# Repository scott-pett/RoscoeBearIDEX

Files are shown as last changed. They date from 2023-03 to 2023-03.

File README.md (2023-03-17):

# Roscoe Bear IDEX 3D Printer

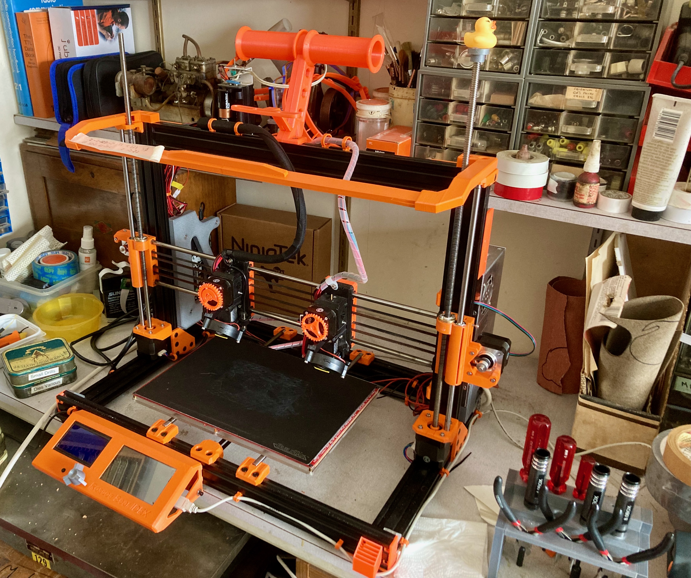
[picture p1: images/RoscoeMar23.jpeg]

__Roscoe Bear IDEX as of March 2023__

This is a remix of @gregsaun's excellent Prusa i3 Bear frame upgrade for the Prusa MK2 and MK3 printers.

I made it wider, taller and use most of the original Bear plastic parts to create a much longer X gantry to make room for a 300mm x 200mm bed and parking space for the two independant extruders. Print height is approximately 230mm, but I'm hoping to improve on that slightly without spending too much money.

# History
The design has been ongoing since 2017 or so and there is now a working prototype albeit lacking in certain features. The prototype has done useful work, but mainly as a single extruder printer :-)

Looking back at some of the design files, things have changed greatly from the earliest concept.

# Electronics and Firmware
The printer currently runs Marlin 2.1.3 and is controlled by a BTT Octopus V1.1 control board with TMC2130 and TMC2208 stepper drivers along with an ancient RepRap Full Graphics Display. A Raspberry Pi 3B+ acts as an Octoprint host and provides WiFi network connectivity and 4.3" touch screen with Octoscreen (or Octodash) for control. The printer can be operated from either screen and files printed from either SD card or via Octoprint. A CSI or USB webcam can be fitted if required.

# Klipper as an option
Of course, Klipper firmware could be used but I feel there would be few advantages except perhaps that of input shaping which has some better capabilities than Marlin2 current has. I doubt there would be much speed advantage being a "bed-slinger" although firmware updates would be more convenient than loading a microSD card into the slot after compiling Marlin in VScode - Horses for Courses.

If you decide to go down the Klipper firmware route, I would be interested in hearing how you get on.

# IDEX Carriages
The main departure from the Prusa Bear design is of course the X and U carriages (AKA: X and X2) which need to allow for the extra U (X2) stepper motor, belt and idler. For the moment this takes the form of taller X carriage components to make room for it all. The printed components comprise the XmotorUidler, UmotorXidler, Xcarriage and Ucarriage. The carriages are formed from two printed parts encapsulating some LM8UU linear bearings in fairly standard Prusa fashion. The arrangement allows for fairly easy assembly of the extruders to the carriages and also allows some early testing with just the carriages fitted. This keeps things fairly clear to setup homing, parking positions and check for clearances.

# Extruders
The X and U extruders are basically Prusa MK3S but with the wiring harness exiting the top of the units - there's not enough room between all the belts to provide the Prusaesque wiring egress. The endstop sensor boards will need their pins bending carefully so the three pin dupont socket attaches vertically rather horiontally. The rest of the assembly is pretty much as per Prusa's build instructions for the MK3S extruder with the ball bearing switched filament sensor. I have not used the earlier MK3 optical sensor variant which sensed filament movement.

The left hand extruder carries a PINDA2 probe for Z homing. This currently runs successfully at 3.3 volts with the spring steel flexplate. The righthand extruder being offset in the Marlin config to allow for any differences. At the moment, this means that the printer will only work in IDEX mode 1 - Auto Park. Mirroring and Cloning (modes 2 and 3) will not be highly successful. A SuperPINDA could be utilized instead. The benefit being that it is temperature compensated and does not rely on a separate thermister setup. So far the PINDA2 has worked fairly reliably.

Filament runout on both extruders is supported as per the Prusa setup. Just utilize a spare endstop port on the Octopus board - see Endstops

# Endstops
X, U and Y endstops are handled by the TMC2130 drivers (TMC2209 as an alternative). Z endstop is, as stated, a PINDA2 probe.

The Endstop configurationis as follows

    X - Xmin (Stallguard)
    U - Xmax (Stallguard)
    Y - Ymin (Stallguard)
    Z - Zmin (PINDA2)
    E0 runout - Zmax
    E1 runout - Ymax

# Thermisters
The BTT Octopus board allows for up to five thermisters. I have them as follows:

    T0 - Hotend 0
    T1 - Hotend 1
    T2 - Reserved for PINDA2 thermister
    T3 - Spare (Maybe for ambient sensor one day)
    TB - Heated Bed

# Heated Bed
The heated bed is a generic 24 volt 300mm x 200mm MK2-B (I think) with a BuildTak flexplate print surface from [3DJake](https://www.3djake.uk)

# Lighting
The Roscoe uses a string of NeoPixels arranged on a bracket above the bed. There is good Marlin support and only one pin is required from the control board. Indeed the BTT Octopus board has a dedicated NeoPixel pin. All that is required is a strong 5V supply to power it. I use a cheap eBay buck converter set to slightly above 5 volts. Marlin can be configured to provide printer events to generate various colours as the printer heats up and successfully completes a job. But this only works when printing from the SD card at the moment. From Octoprint you can just set appropriate commands in the Custom G-code routines to turn the lights on, off and different colours if you wish. Manual control via the menu is also available.

# Work To Do
1. Height adjustment for the U carriage and extruder so IDEX modes 2 and 3 can be used.

2. Purge buckets - and/or a far more reliable purge tower control to improve multi material print quality.

3. Move to Prusaslicer from Cura to improve print quality and simplify configuration - which requirest the next item:

4. Twin part fan control which - Prusaslicer doesn't generate - However, using a post process python script sensible part cooling fan control is available. See the Post Process page.

5. Shorten the height of the X and U carriage to increase the available print height.

6. Switch to a textured PEI sheet from the exisitng BuildTak setup

7. Finalize the Marlin2 config files.

# Alternatives
1. Control board could be a FYSETC Spider board - the Roscoe IDEX requires seven stepper motors to fully enable twin extruders and two independant Z motors. I did originally use an MKS RUMBA32 clone, but this only has support for six steppers and you have to do without the twin Z steppers and automatic gantry levelling. However this can be hacked reasonably well with a gcode script if a RUMBA32 or other six stepper board is all you have.

2. Stepper drivers could be TMC2209 for Stallguard on X, U and Y axis with TMC2208 for the extruders and Z motors. Although TMC have moved on now with driver options, the 22xx series drivers are more than adequate for the motor current requirement. You could always modify the endstop arrangement to something more tradiitonal if that is what you or your budget requires. There's nothing wrong with A4988 drivers and microswitch endstops. But I do like the quietness of the TMC drivers. You can hear the bearings squeak when they dry out!

3. Heated bed - In order to keep the weight down I have used a lightweight PCB heated bed with a flexible spring steel sheet system carrying a BuildTaK print surface. I originally inteneded to fit an aluminium bed carriage - Suitably laser or waterjet cut. But I started building the printer shortly before the first COVID lockdown in 2020 and getting special stuff made became quite difficult - as well as travelling around the country to collect parts. So, my Roscoe Bear IDEX has an acrylic bed carriage. I printed out the DXF outline and stuck it on a sheet of 5mm acrylic and got to work with drills and hacksaw. It is of course a lot lighter than an equivalent aluminium carriage although I doubt it would work too well in an enclosed casing as it would warp when it got hot. Marlin's BiLinear Mesh Bed Levelling appears to work sufficienty well for the moment. Of course a glass sheet and blue tape could be used if that is your preference but will increase the bed weight somewhat. Definitely a candidate for input shaping algorythms of some sort. My favourite, especially for PETG is a textured PEI surface which will be a future upgrade, once I find one - Maybe when the BuildTak surface wears out.

4. Extruder options are of course to use the E3D Revo 6 hotend or a Voron Stealthburner hotend with Clockwork 1 or 2 extruder and blingie RGB LEDs in it. - up to you really. There is a lot of work involved in getting the Stealburner to fit onto the exisitng carriage arrangement though.

5. Another option is to keep the existing MK52 Prusa print bed and make a slightly narrower printer but still have a twin extruder IDEX machine. The standard bed is 250mm wide (instead of 300mm) but offers 210mm in the Y axis (instead of 200mm). Taking 50mm off the X and Top frame members would make the machine slightly more compact.

# Summary 
This is very much a work in progress and is a long way behind things like the BCN3D Sigma and Voron IDEX projects. As a "bed-slinger" its is never going to be as fast as either of the above, but is a fairly simple build from a frame point of view. The open frame means you can see whats goong on and work on the printer fairly easily. The Prusa extruders are fairly easy to build and maintain and there's plenty of life left in the E3D V6 ecosystem. Especially with the new innovative Revo 6 nozzles.

If you have questions or ideas, please contact me.

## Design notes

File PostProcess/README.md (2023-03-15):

This python script is used to post process gcode generation in Prusaslicer 2.5.0. It's function is to rebuild the M106 part cooling fan commands so they correctly turn on (and off) the correct fan.

Prusaslicer does not currently (and as Prusa Research do not produce a multi extruder IDEX machine) is not likely to do so.

This script could also be used in SuperSlicer which is a fork of Prusaslicer - although I've not tested it yet

For users of Cura, one redeeming benefit is that it get the IDEX fan commands correct so fan post processing is not needed - although Cura is lacking in some other areas. If you are a Cura expert, take a look at BCN3D's equivalent setup for their Sigmax IDEX printers

In Prusa Slicer, in the Print Settings tab, under Output Options, enter the path of the Python script into the bottom section.

You will need to have Python3 installed on your system along with any necessary Python modules.

Test manually at first to ensure the paths are setup correctly.

    <pathto>/python3 <pathto>idex_fan_m106.py <pathto>gcodefilename.gcode

It will overwrite the gcode file and you should see something like this:

    M107 P0
    M106 P1 S234
    T1

appearing around the toolchange commands.

If all you're getting is:

    M106 S234

Then it's not working correctly.

This is still a work in progress. I need to test the actual gcode generated extensively.

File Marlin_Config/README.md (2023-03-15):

example Marlin configuration files for Roscoe Bear IDEX printer

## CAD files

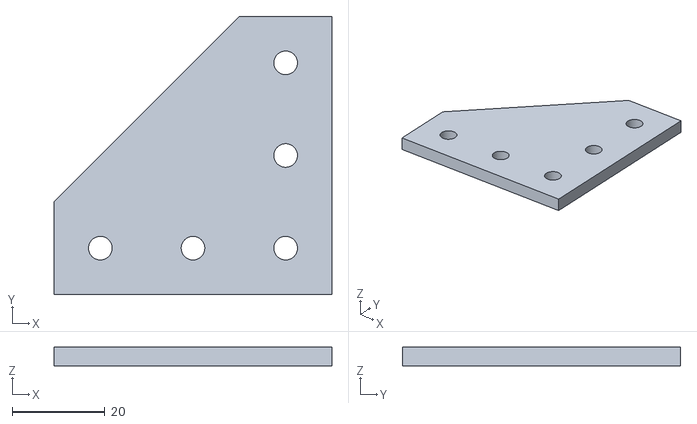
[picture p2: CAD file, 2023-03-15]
PrinterFrame/STL/Joining_Plate_10off_Plain_PETG.stl
60.0 x 60.0 x 4.00

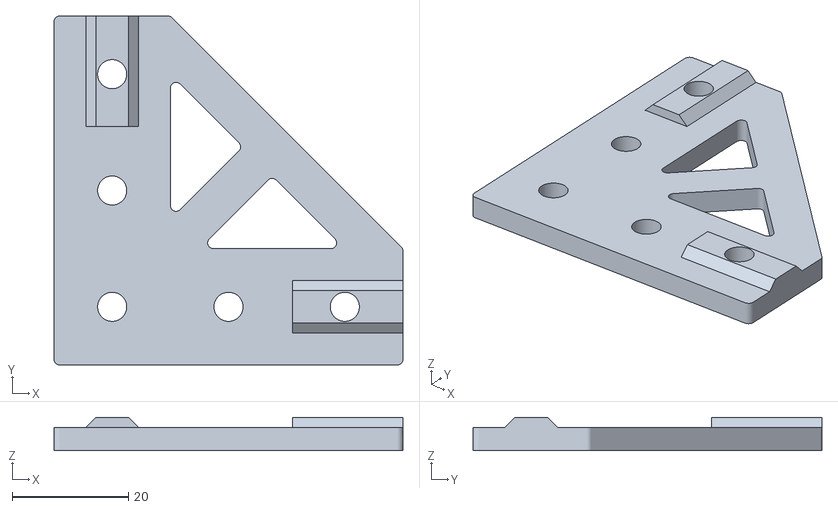
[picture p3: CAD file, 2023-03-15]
PrinterFrame/STL/Joining_Plate_10off_Fancy_PETG.stl
60.0 x 60.0 x 5.70

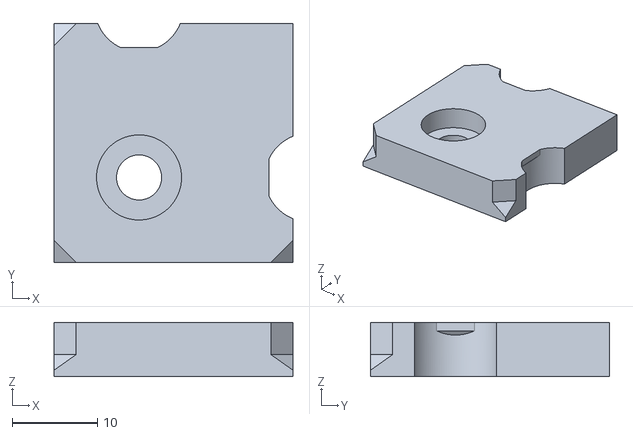
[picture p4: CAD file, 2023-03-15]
PrinterFrame/STL/Foot_4off_TPU.stl
28.1 x 28.1 x 6.40

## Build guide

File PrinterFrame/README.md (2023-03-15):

# The Printer Frame

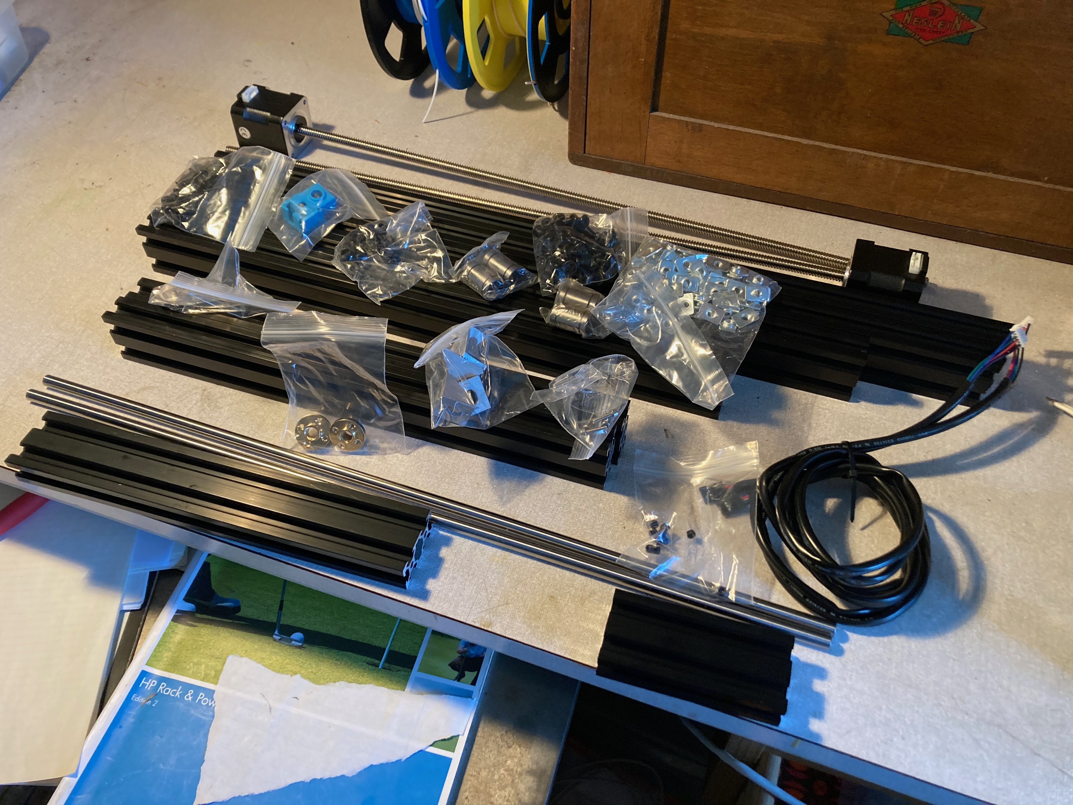
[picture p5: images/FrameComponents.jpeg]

__A Heap of Bits in 2020__

Like the Bear modifications for the Prusa MK3, the frame utilizes fairly typical 2040 aluminium extrusions with either 3D printed or metal brackets and braces. However, the lengths of most of the components are increased to allow for the greater width necessary to park the extruders away from the print bed. This allows each of the extruders to use the full bed area to print. The height is also increased.

When ordering the metalwork it is probably best to obtain the parts pre-cut to length as they need to be cut accurately. My frame components were supplied by [Ooznest](https://ooznest.co.uk) in the UK. I have no links with them other thna a satisfied customer. You will, of course, use your preferred supplier.

Here's a specification for the extrusions:

    X extrusion   570mm long - 2 required
    Y extrusion   331mm long - 2 required
    Z extrusion   415mm long - 2 required
    Top extrusion 490mm long - 1 required

I have found that even at this width, the extruders can get very close to one another and adding 5mm to the X and Top extrusions may make things a little easier space wise.

# Tapping the extrusions
Some of the extrusions may require tapping to take a screw into the ends of the component. In my case only the tops of the Z components required this and it was fairly short work with some grease, a sharp M5 tap and either a steady eye or a tapping guide.

If you have no idea what I'm talking about then your supplier may be able to tap the necessary extrusions prior to despatch.

I will try and include a photograph of the process.

I have found over the years that a decent set of Metric taps has been a useful inclusion in the 3D printing toolkit. I regularly use M3, M4 and M5. M2.5 and M2 occaisionally.

# Printed Parts
In addition you will need 10 off 90º Corner Joining Plates. Mine were 3D printed in PETG and have so far proved strong and resilient enough.

For most of the time, the printed part files can be obtained from @gregsaun's github repository [here:](https://github.com/gregsaun/prusa_i3_bear_upgrade)

Where I have developed different components, or where I use a different print file, they will be found in the STL folder - although they may be OBJ, 3MF or STEP format which are somewhat more robust. If you find issues with any files, please let me know,

So at this point its worth pointing out the flipping obvious, that in the grand 3D printing tradition, you will need access to a 3D printer to create parts for the the new 3D printer. Failing that a 3D print serivce may be availed upon to do the necessary.

The filename format for printed parts goes along the lines of:-

    partname_quantity_option_material

eg: Joining_plate_10off_Plain_PETG.stl

Generally, the materials I use are:- PETG for most of the structural components and a flex or TPU filament for some parts. Of course if you wish and are able to print good quality ABS or ASA components then the print files should be suitable. I tend to stay clear of PLA for structural work like this, although some of the newer PLA+ filaments may prove durable enough. If you ultimately decide to place the printer in an enclosure, then ABS should be preferred but I have used my Prusa clone with PETG parts in an enclosure for some years and it's not fallen apart - yet.

# Fixings
Fixings for the frame are M5 button head screws in various lengths along with M5 Tee nuts. the Bear Bill of Materials (BOM) should be pretty accurate for our needs, but its worth purchasing extras. If you only have enough, then one will invariably disappear behind a box in your workshop. If you purchase spares, then "The Law" says you will not need them. Head here for the [Bear BOM:](https://github.com/gregsaun/prusa_i3_bear_upgrade/blob/master/doc/bom.md)

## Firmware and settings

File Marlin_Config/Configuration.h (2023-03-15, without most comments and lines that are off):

#pragma once
#define CONFIGURATION_H_VERSION 02010300
#define STRING_CONFIG_H_AUTHOR "(ScottP, Roscoe Bear IDEX Config)" // Who made the changes.
#define SHOW_BOOTSCREEN
  #define MOTHERBOARD BOARD_BTT_OCTOPUS_V1_1
#define SERIAL_PORT 1
#define BAUDRATE 115200
#define SERIAL_PORT_2 -1
#define CUSTOM_MACHINE_NAME "Roscoe Octopus IDEX-BF213_MBP"
#define NO_AUTO_ASSIGN_WARNING
#define X_DRIVER_TYPE  TMC2130
#define Y_DRIVER_TYPE  TMC2130
#define Z_DRIVER_TYPE  TMC2208
#define X2_DRIVER_TYPE TMC2130
#define Z2_DRIVER_TYPE TMC2208
#define E0_DRIVER_TYPE TMC2208
#define E1_DRIVER_TYPE TMC2208
#define EXTRUDERS 2
#define DEFAULT_NOMINAL_FILAMENT_DIA 1.75
#define TEMP_SENSOR_0 5
#define TEMP_SENSOR_1 5
#define TEMP_SENSOR_2 0
#define TEMP_SENSOR_3 0
#define TEMP_SENSOR_4 0
#define TEMP_SENSOR_5 0
#define TEMP_SENSOR_6 0
#define TEMP_SENSOR_7 0
#define TEMP_SENSOR_BED 1
#define TEMP_SENSOR_PROBE 0
#define TEMP_SENSOR_CHAMBER 0
#define TEMP_SENSOR_COOLER 0
#define TEMP_SENSOR_BOARD 0
#define TEMP_SENSOR_REDUNDANT 0
#define DUMMY_THERMISTOR_998_VALUE  25
#define DUMMY_THERMISTOR_999_VALUE 100
#if TEMP_SENSOR_IS_MAX_TC(0)
  #define MAX31865_SENSOR_OHMS_0      100 // (Ω) Typically 100 or 1000 (PT100 or PT1000)
  #define MAX31865_CALIBRATION_OHMS_0 430 // (Ω) Typically 430 for Adafruit PT100; 4300 for Adafruit PT1000
#endif
#if TEMP_SENSOR_IS_MAX_TC(1)
  #define MAX31865_SENSOR_OHMS_1      100
  #define MAX31865_CALIBRATION_OHMS_1 430
#endif
#if HAS_E_TEMP_SENSOR
  #define TEMP_RESIDENCY_TIME         10  // (seconds) Time to wait for hotend to "settle" in M109
  #define TEMP_WINDOW                  1  // (°C) Temperature proximity for the "temperature reached" timer
  #define TEMP_HYSTERESIS              3  // (°C) Temperature proximity considered "close enough" to the target
#endif
#if TEMP_SENSOR_BED
  #define TEMP_BED_RESIDENCY_TIME     10  // (seconds) Time to wait for bed to "settle" in M190
  #define TEMP_BED_WINDOW              1  // (°C) Temperature proximity for the "temperature reached" timer
  #define TEMP_BED_HYSTERESIS          3  // (°C) Temperature proximity considered "close enough" to the target
#endif
#if TEMP_SENSOR_CHAMBER
  #define TEMP_CHAMBER_RESIDENCY_TIME 10  // (seconds) Time to wait for chamber to "settle" in M191
  #define TEMP_CHAMBER_WINDOW          1  // (°C) Temperature proximity for the "temperature reached" timer
  #define TEMP_CHAMBER_HYSTERESIS      3  // (°C) Temperature proximity considered "close enough" to the target
#endif
#if TEMP_SENSOR_REDUNDANT
  #define TEMP_SENSOR_REDUNDANT_SOURCE    E1  // The sensor that will provide the redundant reading.
  #define TEMP_SENSOR_REDUNDANT_TARGET    E0  // The sensor that we are providing a redundant reading for.
  #define TEMP_SENSOR_REDUNDANT_MAX_DIFF  10  // (°C) Temperature difference that will trigger a print abort.
#endif
#define HEATER_0_MINTEMP   5
#define HEATER_1_MINTEMP   5
#define HEATER_2_MINTEMP   5
#define HEATER_3_MINTEMP   5
#define HEATER_4_MINTEMP   5
#define HEATER_5_MINTEMP   5
#define HEATER_6_MINTEMP   5
#define HEATER_7_MINTEMP   5
#define BED_MINTEMP        5
#define CHAMBER_MINTEMP    5
#define HEATER_0_MAXTEMP 275
#define HEATER_1_MAXTEMP 275
#define HEATER_2_MAXTEMP 275
#define HEATER_3_MAXTEMP 275
#define HEATER_4_MAXTEMP 275
#define HEATER_5_MAXTEMP 275
#define HEATER_6_MAXTEMP 275
#define HEATER_7_MAXTEMP 275
#define BED_MAXTEMP      120
#define CHAMBER_MAXTEMP  60
#define HOTEND_OVERSHOOT 15   // (°C) Forbid temperatures over MAXTEMP - OVERSHOOT
#define BED_OVERSHOOT    10   // (°C) Forbid temperatures over MAXTEMP - OVERSHOOT
#define COOLER_OVERSHOOT  2   // (°C) Forbid temperatures closer than OVERSHOOT
#define PIDTEMP          // See the PID Tuning Guide at https://reprap.org/wiki/PID_Tuning
#define BANG_MAX 255     // Limits current to nozzle while in bang-bang mode; 255=full current
#define PID_MAX BANG_MAX // Limits current to nozzle while PID is active (see PID_FUNCTIONAL_RANGE below); 255=full current
#define PID_K1 0.95      // Smoothing factor within any PID loop
  #define PID_PARAMS_PER_HOTEND // Use separate PID parameters for each extruder (useful for mismatched extruders)
    #define DEFAULT_Kp_LIST {  24.45,  23.96 }
    #define DEFAULT_Ki_LIST {   2.47,   2.40 }
    #define DEFAULT_Kd_LIST {  60.59, 59.84 }
#define PIDTEMPBED
#define MAX_BED_POWER 255 // limits duty cycle to bed; 255=full current
  #define DEFAULT_bedKp 143.5702 // was 156.24
  #define DEFAULT_bedKi 16.7801  // was 20.56
  #define DEFAULT_bedKd 818.9247 // was 791.60
#define MAX_CHAMBER_POWER 255 // limits duty cycle to chamber heater; 255=full current
  #define PID_FUNCTIONAL_RANGE 10 // If the temperature difference between the target temperature and the actual temperature
  #define PID_EDIT_MENU         // Add PID editing to the "Advanced Settings" menu. (~700 bytes of flash)
  #define PID_AUTOTUNE_MENU     // Add PID auto-tuning to the "Advanced Settings" menu. (~250 bytes of flash)
#define PREVENT_COLD_EXTRUSION
#define EXTRUDE_MINTEMP 170
#define PREVENT_LENGTHY_EXTRUDE
#define EXTRUDE_MAXLENGTH 200
#define THERMAL_PROTECTION_HOTENDS // Enable thermal protection for all extruders
#define THERMAL_PROTECTION_BED     // Enable thermal protection for the heated bed
#define THERMAL_PROTECTION_CHAMBER // Enable thermal protection for the heated chamber
#define THERMAL_PROTECTION_COOLER  // Enable thermal protection for the laser cooling
#define USE_XMIN_PLUG
#define USE_YMIN_PLUG
#define USE_XMAX_PLUG
#define ENDSTOPPULLUPS
#define X_MIN_ENDSTOP_INVERTING true // Set to true to invert the logic of the endstop.
#define Y_MIN_ENDSTOP_INVERTING true // Set to true to invert the logic of the endstop.
#define Z_MIN_ENDSTOP_INVERTING false // Set to true to invert the logic of the endstop.
#define I_MIN_ENDSTOP_INVERTING false // Set to true to invert the logic of the endstop.
#define J_MIN_ENDSTOP_INVERTING false // Set to true to invert the logic of the endstop.
#define K_MIN_ENDSTOP_INVERTING false // Set to true to invert the logic of the endstop.
#define U_MIN_ENDSTOP_INVERTING false // Set to true to invert the logic of the endstop.
#define V_MIN_ENDSTOP_INVERTING false // Set to true to invert the logic of the endstop.
#define W_MIN_ENDSTOP_INVERTING false // Set to true to invert the logic of the endstop.
#define X_MAX_ENDSTOP_INVERTING true // Set to true to invert the logic of the endstop.
#define Y_MAX_ENDSTOP_INVERTING false // Set to true to invert the logic of the endstop.
#define Z_MAX_ENDSTOP_INVERTING false // Set to true to invert the logic of the endstop.
#define I_MAX_ENDSTOP_INVERTING false // Set to true to invert the logic of the endstop.
#define J_MAX_ENDSTOP_INVERTING false // Set to true to invert the logic of the endstop.
#define K_MAX_ENDSTOP_INVERTING false // Set to true to invert the logic of the endstop.
#define U_MAX_ENDSTOP_INVERTING false // Set to true to invert the logic of the endstop.
#define V_MAX_ENDSTOP_INVERTING false // Set to true to invert the logic of the endstop.
#define W_MAX_ENDSTOP_INVERTING false // Set to true to invert the logic of the endstop.
#define Z_MIN_PROBE_ENDSTOP_INVERTING false // Set to true to invert the logic of the probe.
#define ENDSTOP_INTERRUPTS_FEATURE
#define DISTINCT_E_FACTORS
#define DEFAULT_AXIS_STEPS_PER_UNIT   { 100, 100, 400, 142.5, 142.5 }
#define DEFAULT_MAX_FEEDRATE          { 200, 200, 12, 25, 25 }
#define LIMITED_MAX_FR_EDITING        // Limit edit via M203 or LCD to DEFAULT_MAX_FEEDRATE * 2
  #define MAX_FEEDRATE_EDIT_VALUES    { 600, 600, 10, 50 } // ...or, set your own edit limits
#define DEFAULT_MAX_ACCELERATION      { 1500, 1500, 50, 2000, 2000 }
#define DEFAULT_ACCELERATION          2000    // X, Y, Z and E acceleration for printing moves
#define DEFAULT_RETRACT_ACCELERATION  3000    // E acceleration for retracts
#define DEFAULT_TRAVEL_ACCELERATION   2000    // X, Y, Z acceleration for travel (non printing) moves
#define CLASSIC_JERK
  #define DEFAULT_XJERK 12.0
  #define DEFAULT_YJERK 12.0
  #define DEFAULT_ZJERK  0.4
#define DEFAULT_EJERK    10.0  // May be used by Linear Advance
#define S_CURVE_ACCELERATION
#define USE_PROBE_FOR_Z_HOMING
#define Z_MIN_PROBE_PIN PG10 // Pin 32 is the RAMPS default
#define FIX_MOUNTED_PROBE
#define NOZZLE_TO_PROBE_OFFSET { 23, 7, -0.100 }
#define PROBING_MARGIN 10
#define XY_PROBE_FEEDRATE (133*60)
#define Z_PROBE_FEEDRATE_FAST (12*60)
#define Z_PROBE_FEEDRATE_SLOW (Z_PROBE_FEEDRATE_FAST / 3)
#define MULTIPLE_PROBING 2
#define Z_CLEARANCE_DEPLOY_PROBE   10 // Z Clearance for Deploy/Stow
#define Z_CLEARANCE_BETWEEN_PROBES  5 // Z Clearance between probe points
#define Z_CLEARANCE_MULTI_PROBE     5 // Z Clearance between multiple probes
#define Z_PROBE_LOW_POINT          -2 // Farthest distance below the trigger-point to go before stopping
#define Z_PROBE_OFFSET_RANGE_MIN -20
#define Z_PROBE_OFFSET_RANGE_MAX 20
#define Z_MIN_PROBE_REPEATABILITY_TEST
#define X_ENABLE_ON 0
#define Y_ENABLE_ON 0
#define Z_ENABLE_ON 0
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

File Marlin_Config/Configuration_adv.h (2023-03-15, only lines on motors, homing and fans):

  #define CONTROLLER_FAN_PIN PD14           // Set a custom pin for the controller fan
#define E0_AUTO_FAN_PIN PA8
#define E1_AUTO_FAN_PIN PD12
#define E2_AUTO_FAN_PIN -1
#define E3_AUTO_FAN_PIN -1
#define E4_AUTO_FAN_PIN -1
#define E5_AUTO_FAN_PIN -1
#define E6_AUTO_FAN_PIN -1
#define E7_AUTO_FAN_PIN -1
#define CHAMBER_AUTO_FAN_PIN -1
#define COOLER_AUTO_FAN_PIN -1
#define DUAL_X_CARRIAGE
  #define X2_HOME_DIR    1        // Set to 1. The X2 carriage always homes to the max endstop position
  #define X2_HOME_POS X2_MAX_POS  // Default X2 home position. Set to X2_MAX_POS.
  #define DEFAULT_DUAL_X_CARRIAGE_MODE DXC_AUTO_PARK_MODE
#define HOMING_BUMP_MM      { 0, 0, 2 }       // (linear=mm, rotational=°) Backoff from endstops after first bump
#define HOMING_BUMP_DIVISOR { 2, 2, 4 }       // Re-Bump Speed Divisor (Divides the Homing Feedrate)
#define HOMING_BACKOFF_POST_MM { 0, 0, 0 }  // (linear=mm, rotational=°) Backoff from endstops after homing
  #define HOME_AFTER_G34
#define MICROSTEP_MODES { 16, 16, 16, 16, 16, 16 } // [1,2,4,8,16]
#define LIN_ADVANCE
    #define ADVANCE_K { 0.22 }    // (mm) Compression length per 1mm/s extruder speed, per extruder
#define ADVANCED_PAUSE_FEATURE
  #define ADVANCED_PAUSE_PURGE_FEEDRATE        3  // (mm/s) Extrude feedrate (after loading). Should be slower than load feedrate.
  #define ADVANCED_PAUSE_PURGE_LENGTH         50  // (mm) Length to extrude after loading.
  #define ADVANCED_PAUSE_RESUME_PRIME          0  // (mm) Extra distance to prime nozzle after returning from park.
    #define X_CURRENT       1000        // (mA) RMS current. Multiply by 1.414 for peak current.
    #define X_CURRENT_HOME  X_CURRENT  // (mA) RMS current for sensorless homing
    #define X_MICROSTEPS     16        // 0..256
    #define X2_CURRENT      1000
    #define X2_CURRENT_HOME X2_CURRENT
    #define X2_MICROSTEPS    X_MICROSTEPS
    #define Y_CURRENT      1000
    #define Y_CURRENT_HOME  Y_CURRENT
    #define Y_MICROSTEPS     16
    #define Z_CURRENT       800
    #define Z_CURRENT_HOME  Z_CURRENT
    #define Z_MICROSTEPS     16
    #define Z2_CURRENT      800
    #define Z2_CURRENT_HOME Z2_CURRENT
    #define Z2_MICROSTEPS    Z_MICROSTEPS
    #define E0_CURRENT      800
    #define E0_MICROSTEPS    16
    #define E1_CURRENT      800
    #define E1_MICROSTEPS   E0_MICROSTEPS
    #define CURRENT_STEP_DOWN     50  // [mA]
    #define REPORT_CURRENT_CHANGE
  #define HYBRID_THRESHOLD
  #define X_HYBRID_THRESHOLD     100  // [mm/s]
  #define X2_HYBRID_THRESHOLD    100
  #define Y_HYBRID_THRESHOLD     100
  #define Y2_HYBRID_THRESHOLD    100
  #define Z_HYBRID_THRESHOLD       13
  #define Z2_HYBRID_THRESHOLD      13
  #define Z3_HYBRID_THRESHOLD      3
  #define Z4_HYBRID_THRESHOLD      3
  #define I_HYBRID_THRESHOLD       3  // [linear=mm/s, rotational=°/s]
  #define J_HYBRID_THRESHOLD       3  // [linear=mm/s, rotational=°/s]
  #define K_HYBRID_THRESHOLD       3  // [linear=mm/s, rotational=°/s]
  #define U_HYBRID_THRESHOLD       3  // [mm/s]
  #define V_HYBRID_THRESHOLD       3
  #define W_HYBRID_THRESHOLD       3
  #define E0_HYBRID_THRESHOLD     30
  #define E1_HYBRID_THRESHOLD     30
  #define E2_HYBRID_THRESHOLD     30
  #define E3_HYBRID_THRESHOLD     30
  #define E4_HYBRID_THRESHOLD     30
  #define E5_HYBRID_THRESHOLD     30
  #define E6_HYBRID_THRESHOLD     30
  #define E7_HYBRID_THRESHOLD     30
  #define SENSORLESS_HOMING // StallGuard capable drivers only
    #define X_STALL_SENSITIVITY  1
    #define X2_STALL_SENSITIVITY 1
    #define Y_STALL_SENSITIVITY  1
    #define Y2_STALL_SENSITIVITY Y_STALL_SENSITIVITY

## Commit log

2023-03-15 add Marlin configuration files
    [Configuration.h, Configuration_adv.h]
2023-03-15 add readme for Marlin config files
2023-03-15 add printer frame description
2023-03-15 Frame Readme update
2023-03-15 STL updates
    [Foot_4off_TPU.stl]

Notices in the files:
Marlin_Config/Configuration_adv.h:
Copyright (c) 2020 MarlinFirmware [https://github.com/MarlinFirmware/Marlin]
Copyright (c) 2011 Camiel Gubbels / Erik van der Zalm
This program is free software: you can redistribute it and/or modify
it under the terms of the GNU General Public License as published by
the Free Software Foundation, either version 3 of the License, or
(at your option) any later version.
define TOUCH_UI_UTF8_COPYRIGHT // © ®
